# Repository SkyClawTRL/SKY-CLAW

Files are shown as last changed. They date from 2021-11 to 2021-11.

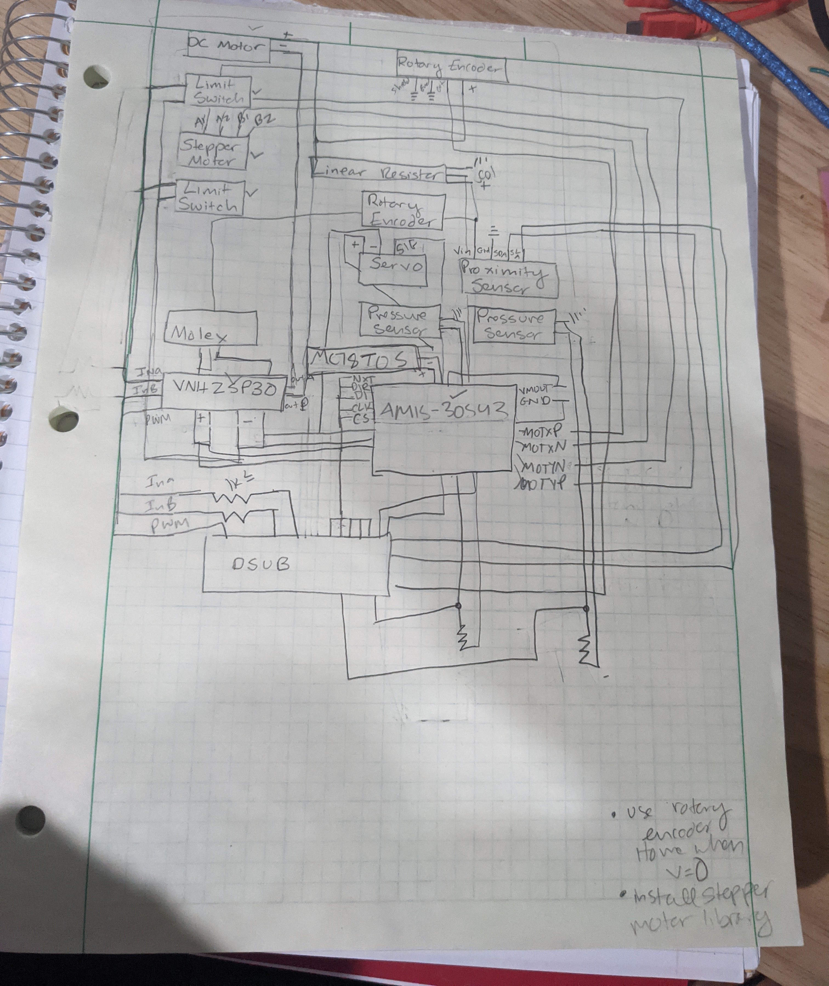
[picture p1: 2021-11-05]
Schematics and Datasheets/CONTROL BOX SCHEMATIC.jpg

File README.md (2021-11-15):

# SKY-CLAW
Fully Open Source Gantry-Style Robotic Gripper
The claw is a four degree of freedom robot equipped with multiple sensors and actuators. The four degrees of freedom are horizontal translation, vertical translation, (passive) rotation, and grasping motion. The claw is similar to a gantry crane that might be found at a construction site or in a warehouse. The purpose of this project is to provide an educational platform for teaching mechatronics. The benefits of this platform are:
  a) It provides a diverse set of sensors and actuators:
       i) Sensors: limit switches, proximity sensor, linear potentiometer, rotary encoders.
       ii) Actuators: Stepper motor, brushed DC motor, servo
  b) It is 100% open source and uses common commercial off-the-shelf components and complete solid models of all parts including drawings of custom-made parts.
  c) All custom-made components are easy to manufacture. If a student breaks it, he or she can also repair it.

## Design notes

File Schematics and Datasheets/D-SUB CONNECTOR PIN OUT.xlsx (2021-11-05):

1 | Proximity Sensor | SDA (Blue)
2 | Servo | Positive (Yellow)
3 | VNH25P30 Driver | PWM (Blue)
4 | VNH25P30 Driver | In A (Green)
5 | VNH25P30 Driver | In B (White)
6 | AMIS-30543 Driver | Nxt/Step (Blue)
7 | AMIS-30543 Driver | DIR (Blue)
8 | AMIS-30543 Driver | CLK (Green)
9 | AMIS-30543 Driver | DI (Green)
10 | AMIS-30543 Driver | CS ( Green)
11 | Pressure Sensor 1 | Voltage Divider (Green)
12 | Pressure Sensor 2 | Voltage Divider (White)
13 | Proximity Sensor | SCL (white)
14 | nc | nc
15 | nc | nc
16 | nc | nc
17 | nc | nc
18 | nc | nc
19 | nc | nc
20 | Ground | Black
21 | Linear Resistor | Col (White)
22 | Top Rotary Encoder | Channel A (black)
23 | Top Rotary Encoder | Channel B (white)
24 | Claw Rotary Encoder | Channel B (White)
25 | Claw Rotary Encoder | Channel A (Black)

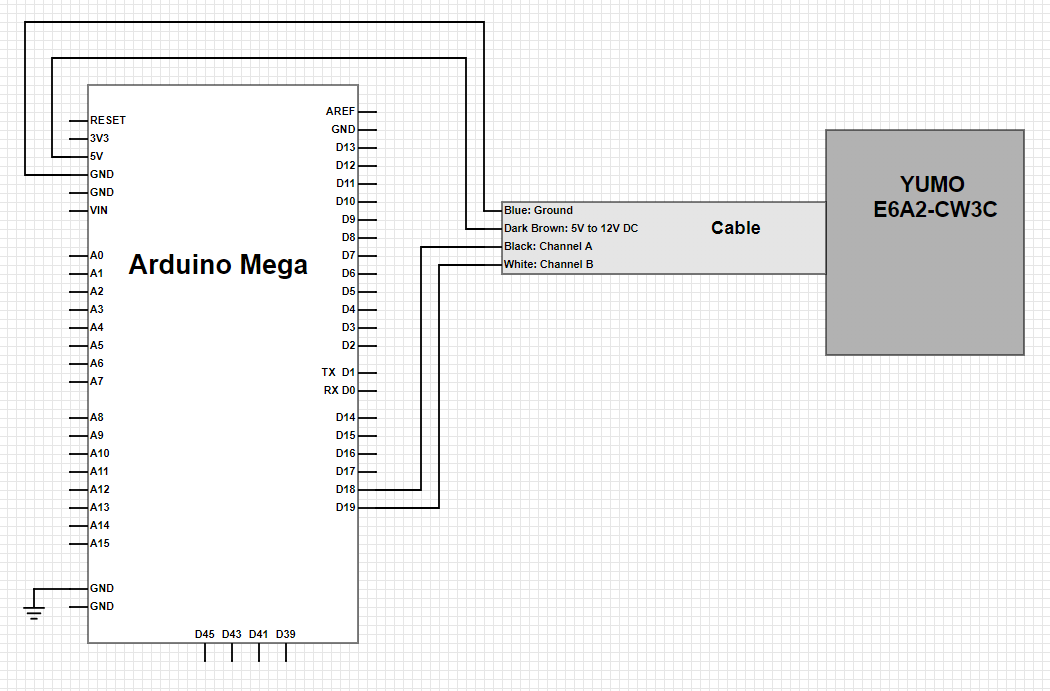
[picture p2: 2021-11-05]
Schematics and Datasheets/Yumo E6A2-CW3C Rotary Encoder Schematic.PNG

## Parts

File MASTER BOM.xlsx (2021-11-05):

PART NUMBER | SUPPLIER | DESCRIPTION | QUANTITY | PRICE | TOTAL COST | NOTES
2191A14 | Mc-Master-Carr | Steel Metric Ball-Nose Plunger with Plastic Nose M6x1 Thread, 6.3-9 lb. Nose Force | 1 | $5.54 | $5.54
4575N23 | Mc-Master-Carr | Light Duty Mounted Ball Bearing with Two-Bolt Flange, Open, for 1/4" Shaft Diameter | 13 | $9.70 | $126.10
47065T101 | Mc-Master-Carr | T-Slotted Framing Single Four Slot Rail, Silver, 1" High x 1" Wide, Solid 4 Feet Long | 2 | $18.05 | $36.10
47065T139 | Mc-Master-Carr | T-Slotted Framing End-Feed Single Nut with Button Head 1/4"-20 Thread Size | 44 | $2.22 | $24.42
47065T236 | Mc-Master-Carr | Silver Corner Bracket, 1" Long for 1" High Rail T-Slotted Framing | 12 | $5.63 | $67.56
57155K336 | Mc-Master-Carr | Stainless Steel Ball Bearing Flanged, Shielded with Extended Inner Ring, Number R168-2Z | 3 | $7.35 | $22.05
6477K58 | Mc-Master-Carr | Two Arm Knob Black Nylon, 1/4"-20 Threaded Through-Hole | 1 | $1.23 | $1.23
6484K454 | Mc-Master-Carr | XL Series Timing Belt, Trade No. 770XL037 3/8" Thick | 1 | $20.26 | $20.26
7565K46 | Mc-Master-Carr | Cable Holders Adhesive-Back, Nylong, 1" Long x 3/4" Wide x 7/8" High | 7 | $9.05 | $9.05
8505K754 | Mc-Master-Carr | Scratch-Resistant Acrylic, 12" x 12" x 1/4" | 1 | $10.78 | $10.78
8632T141 | Mc-Master-Carr | D-Profile Rotary Shaft 1045 Carbon Steel, 1/4" Diameteer, 24" Long | 5 | $16.50 | $16.50
8975K468 | Mc-Master-Carr | 6061 Aluminum 3/8" Thick x 2-1/2" Wide Sheet and Bar 3 Feet Long | 3 | $26.37 | $79.11
9001K62 | Mc-Master-Carr | 6063 Aluminum U-Channel 1/8" Wall Thickness, 2" High x 1-1/2" Wide | 1 | $43.88 | $43.88
90480A007 | Mc-Master-Carr | Low-Strength Steel Hex Nut Zinc-Plated, 6-32 Thread Size | 74 | $1.28 | $1.28
90633A005 | Mc-Master-Carr | Low-Strength Steel Thin Nylon-Insert Locknut Zinc-Plated, 4-40 Thread Size | 2 | $3.71 | $3.71
90695A038 | Mc-Master-Carr | Steel Thin Hex Nut Medium-Strength, Zinc-Plated, M6x1mm Thread | 2 | $3.45 | $3.45
90730A003 | Mc-Master-Carr | 18-8 Stainless Steel Narrow Hex Nut 2-56 Thread Size | 2 | $3.66 | $3.66
91239A115 | Mc-Master-Carr | Button Head Hex Drive Screw Black-Oxide Alloy Steel, M3x0.50mm Thread, 10mm Long | 8 | $8.12 | $8.12
91255A539 | Mc-Master-Carr | Button Head Hex Drive Screw Black-Oxide Alloy Steel, 1/4"-20 Thread, 5/8" Long | 18 | $9.78 | $9.78
91292A025 | Mc-Master-Carr | 18-8 Stainless Steel Socket Head Screw M3x0.50mm Thread, 45mm Long | 8 | $12.76 | $12.76
91772A361 | Mc-Master-Carr | Passivated 18-8 Stainless Steel Pan Head Phillips Screw 8-32 Thread, 1-5/8" Long | 4 | $8.85 | $8.85
91772A544 | Mc-Master-Carr | Passivated 18-8 Stainless Steel Pan Head Phillips Screw 1/4"-20 Thread, 1-1/4" Long | 4 | $7.97 | $7.97
91841A005 | Mc-Master-Carr | 18-8 Stainless Steel Hex Nut 4-40 Thread Size | 5 | $2.82 | $2.82
91841A009 | Mc-Master-Carr | 18-8 Stainless Steel Hex Nut 8-32 Thread Size | 38 | $3.46 | $3.46
91845A029 | Mc-Master-Carr | 18-8 Stainless Steel Hex Nut 1/4"-20 Thread Size | 8 | $3.85 | $3.85
92196A149 | Mc-Master-Carr | 18-8 Stainless Steel Socket Head Screw 6-32 Thread Size, 9/16" Long | 8 | $12.65 | $12.65
92196A194 | Mc-Master-Carr | 18-8 Stainless Steel Socket Head Screw 8-32 Thread Size, 1/2" Long | 10 | $6.24 | $6.24
92210A196 | Mc-Master-Carr | 18-8 Stainless Steel Hex Drive Flat Head Screw 8-32 Thread Size, 5/8" Long | 22 | $5.90 | $5.90
92949A079 | Mc-Master-Carr | 18-8 Stainless Steel Button Head Hex Drive Screw 2-56 Thread Size, 3/8" Long | 2 | $6.59 | $6.59
92949A110 | Mc-Master-Carr | 18-8 Stainless Steel Button Head Hex Drive Screw 4-40 Thread Size, 1/2" Long | 3 | $3.38 | $3.38
92949A116 | Mc-Master-Carr | 18-8 Stainless Steel Button Head Hex Drive Screw 4-40 Thread Size, 1" Long | 4 | $4.75 | $4.75
92949A144 | Mc-Master-Carr | 18-8 Stainless Steel Button Head Hex Drive Screw 6-32 Thread Size, 1/4" Long | 4 | $3.45 | $3.45
92949A150 | Mc-Master-Carr | 18-8 Stainless Steel Button Head Hex Drive Screw 6-32 Thread Size, 5/8" Long | 84 | $4.07 | $4.07
92949A153 | Mc-Master-Carr | 18-8 Stainless Steel Button Head Hex Drive Screw 6-32 Thread Size, 1" Long | 18 | $5.42 | $5.42
92949A157 | Mc-Master-Carr | 18-8 Stainless Steel Button Head Hex Drive Screw 6-32 Thread Size, 1-1/2" Long | 2 | $4.58 | $4.58
92949A205 | Mc-Master-Carr | 18-8 Stainless Steel Button Head Hex Drive Screw 8-32 Thread Size, 1-3/4" Long | 4 | $8.66 | $8.66
93330A471 | Mc-Master-Carr | Female Threaded Round Standoff Aluminum, 1/4" OD, 1-1/4" Long, 6-32 Thread Size | 2 | $1.23 | $2.46
93548A550 | Mc-Master-Carr | Zinc-Plated Grade 2 Steel Square-Neck Carriage Bolt Low-Strength, 1/4"-20 Thread Size, 2" Long | 1 | $10.75 | $10.75
94639A297 | Mc-Master-Carr | Off-White Nylon Unthreaded Spacer 1/4" OD, 3/4" Long, for Number 8 Screw Size | 4 | $12.47 | $12.47
94639A298 | Mc-Master-Carr | Off-White Nylon Unthreaded Spacer 1/4" OD, 1" Long, for Number 8 Screw Size | 4 | $13.56 | $13.56
94639A300 | Mc-Master-Carr | Off-White Nylon Unthreaded Spacer 1/4" OD, 3/16" Long, for Number 6 Screw Size | 6 | $10.35 | $10.35
94639A569 | Mc-Master-Carr | Off-White Nylon Unthreaded Spacer 1/2" OD, 1/4" Long, for 1/4" Screw Size | 14 | $11.38 | $11.38
9880K13 | Mc-Master-Carr | 15mm Wide Guide Rail for High-Temperature Sleeve Bearing Carriage 670mm Long | 2 | $122.61 | $245.22
9880K3 | Mc-Master-Carr | High-Temperature Sleeve Bearing Carriage for 15mm Wide Rail | 2 | $54.40 | $108.80
LPM80-180-1(318025)-c | PBC Linear | Nylon Slider | 1 | $25.23 | $25.23
LPM80R-0780 | PBC Linear | Aluminum Rail Y=16mm | 1 | $94.56 | $94.56
LSSSSR-037-0250-FY24 | HaydenKerk | 3/8" Lead Screw | 2 | $51.16 | $102.32
BFWFNR-037-0250-BZ00 | HaydenKerk | Lead Screw Nut | 2 | $16.18 | $32.36
14203S009-SP | HaydenKerk | 24V Brushed DC Motor | 1 | $184.80 | $184.80
2267 | Pololu | NEMA 17 Stepper Motor | 1 | $17.95 | $17.95
1212 | Pololu | MC33926 Motor Driver Carrier | 1 | $17.95 | $17.95
744-SP-L-0750-2033ST | Mouser | Linear Resistor | 1 | $45.07 | $45.07
782-A000067 | Mouser | Arduino Mega | 1 | $38.50 | $38.50
COM-10932 | SparkFun | Yumo E6A2-CW3C | 2 | $44.95 | $89.90
COM-11992 | SparkFun | Momentary Button | 2 | $0.95 | $1.90
ROB-12156 | SparkFun | Timing Belt - XL (per foot) 6 Feet Long | 6 | $3.59 | $21.54
ROB-12251 | SparkFun | Shaft Coupler - 1/4" to 1/4" | 4 | $4.99 | $19.96
ROB-12325 | SparkFun | Shaft Coupler - 1/4" to 5mm | 1 | $4.99 | $4.99
ROB-12347 | SparkFun | Servo Block Kit - Hitec Standard (Hub Shaft) | 1 | $26.99 | $26.99
ROB-12488 | SparkFun | Set Screw Hub | 4 | $4.99 | $19.96
ROB-12493 | SparkFun | Shaft Coupler - 1/4" to 4mm | 1 | $4.99 | $4.99
ROB-13597 | SparkFun | Timing Pulley - Shaft Mount (15T; 0.25" Bore) | 5 | $8.95 | $44.75
SEN-08712 | SparkFun | FlexiForce Pressure Sensor - 25lbs. | 2 | $21.95 | $43.90
35645S00 | Servo City | HS-5645MG Servo | 1 | $44.99 | $44.99
SC508 | Servo City | Servo Connector Pack Hitec Male/Female Set | 1 | $2.99 | $2.99
SW22JT | Servo City | Super Duty Servo Wire 50 Feet Long | 1 | $12.99 | $12.99
1508102 | Home Depot | 1/4 in x 2 ft x 2 ft MDF Panel | 2 | $8.85 | $17.70
466 | Adafruit | VCNL4010 Proximity Sensor | 1 | $7.50 | $7.50
SMAKN TB6600 | Amazon | 4A 40V 57/86 Stepper Motor Driver | 1 | $14.90 | $14.90
Ginsco | Amazon | 580 pieces Heat Shrink Tubing Kit 6 Colors 11 Sizes | 1 | $5.99 | $5.99
Striveday | Amazon | Flexible Silicon Wire 22awg Electric Wire 22 Gauge Copper 330V | 1 | $15.99 | $15.99
EDGELEC | Amazon | Multicolored Breadboard Jumper Wires Assorted Kit 120 pieces | 1 | $5.77 | $5.77
 |  |  |  | Total | $1979.41 | Pricing was done on 7/11/2021

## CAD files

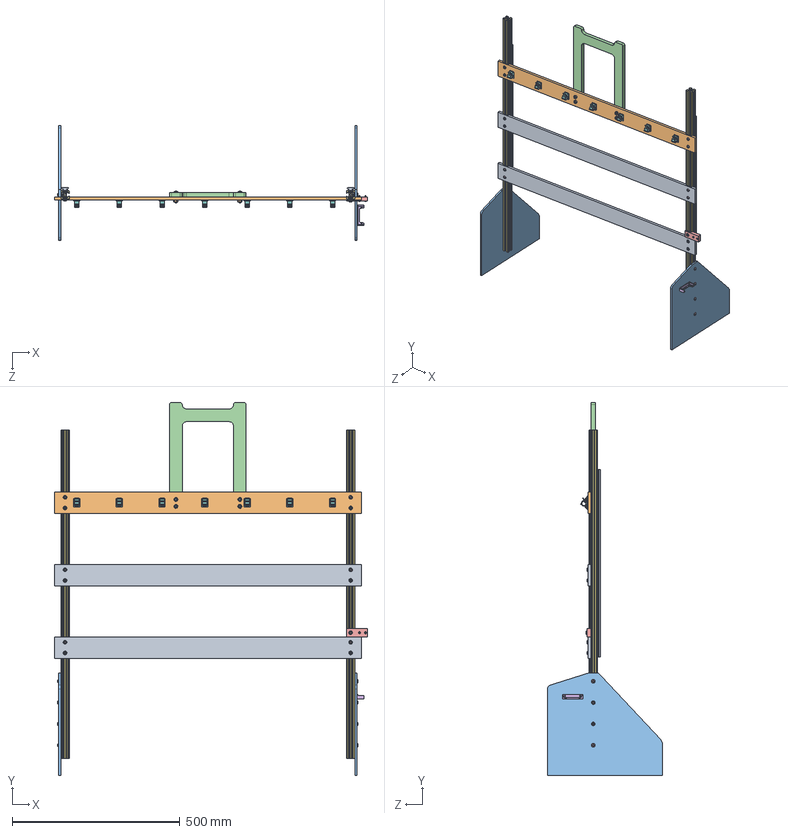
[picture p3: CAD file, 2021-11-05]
SUBASSEMBLIES/FRAME ASSEMBLY.SLDASM
933.2 x 1111.2 x 342.9 mm
FRAME BRACE x 2
FRAME BRACE TOP
FOOT x 2
HANDLE
CABLE CARRIER CONNECTOR VERTICAL
DSUB MOUNT
47065T101_ALUMINUM T-SLOTTED FRAMING EXTRUSION x 2
7565K460_CABLE HOLDERS x 7
9880K135_SLEEVE BEARING CARRIAGE x 2
91845A029_TYPE 18-8 STAINLESS STEEL HEX NUT x 4
91772A544_18-8 SS PAN HEAD PHILLIPS MACHINE SCREW x 4
92949A150_18-8 SS BUTTON-HEAD SOCKET CAP SCREW x 2
47065T139_ALUMINUM T-SLOTTED FRAMING EXTRUSION x 35

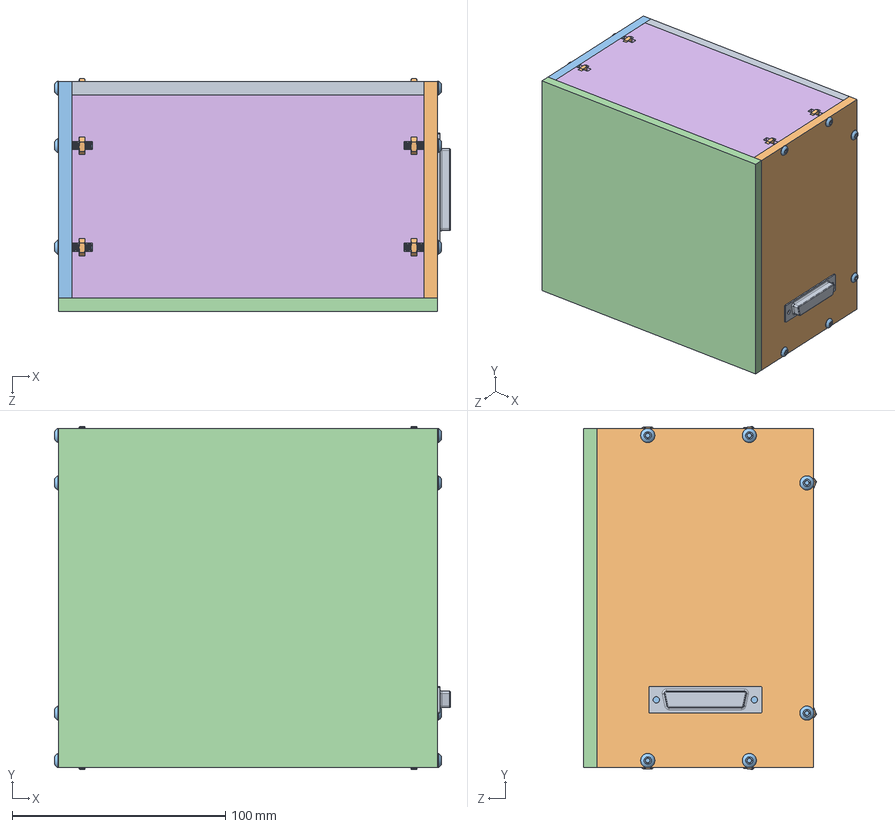
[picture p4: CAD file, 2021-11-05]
SUBASSEMBLIES/CONTROL BOX.SLDASM
185.7 x 160.9 x 109.3 mm
CONTROL BOX BACK PANEL
CONTROL BOX RIGHT PANEL
CONTROL BOX LEFT PANEL
CONTROL BOX FRONT PANEL
CONTROL BOX BOTTOM PANEL
CONTROL BOX TOP PANEL
VNH3SP30 Motor Driver Carrier MD01B x 2
PCB
D-SUB CONNECTOR
90480A007_LOW-STRENGTH STEEL HEX NUT x 12
92949A150_18-8 SS BUTTON-HEAD SOCKET CAP SCREW x 12

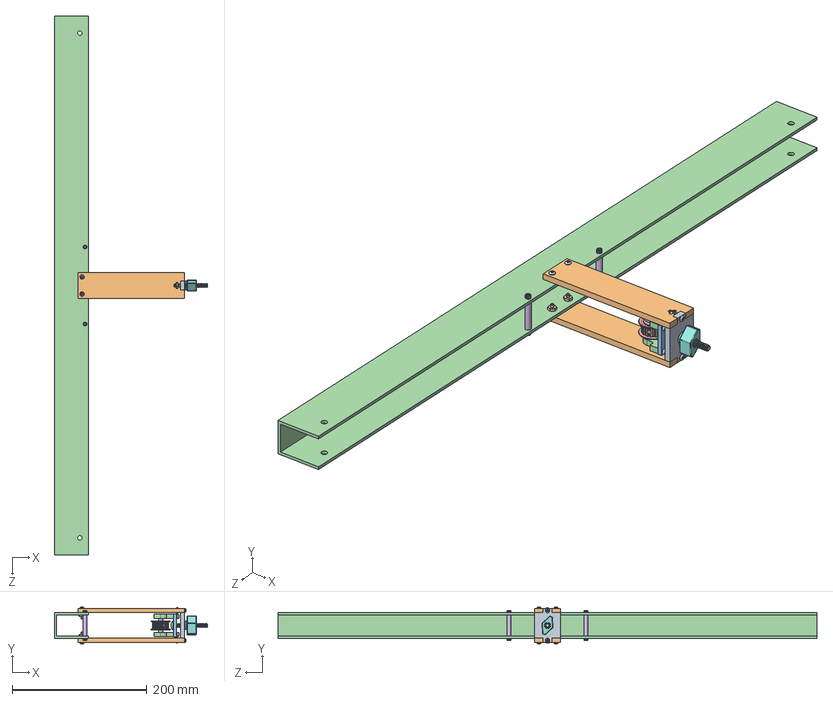
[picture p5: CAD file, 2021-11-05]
SUBASSEMBLIES/U-CHANNEL ASSEMBLY.SLDASM
227.8 x 54.5 x 800.1 mm
TENSIONER SUPPORT BACK
TENSIONER SUPPORT BASE x 2
TENSIONER PLATE
TENSIONER BEARING x 2
ROB-13597 TIMING PULLEY
8632T141_D-SHAFT PROFILE 1.3125 LG
tensioner bolt_93548A550
tensioner knob 6477K580
92949A150_18-8 SS BUTTON-HEAD SOCKET CAP SCREW x 6
90480A007_LOW-STRENGTH STEEL HEX NUT x 6
caseing screw 92185A164 x 4
TENSIONER U-CHANNEL
92196A149_18-8 STAINLESS STEEL SOCKET HEAD SCREW x 4
93330A471_ALUM FEM THRDED ROUND STANDOFF x 2

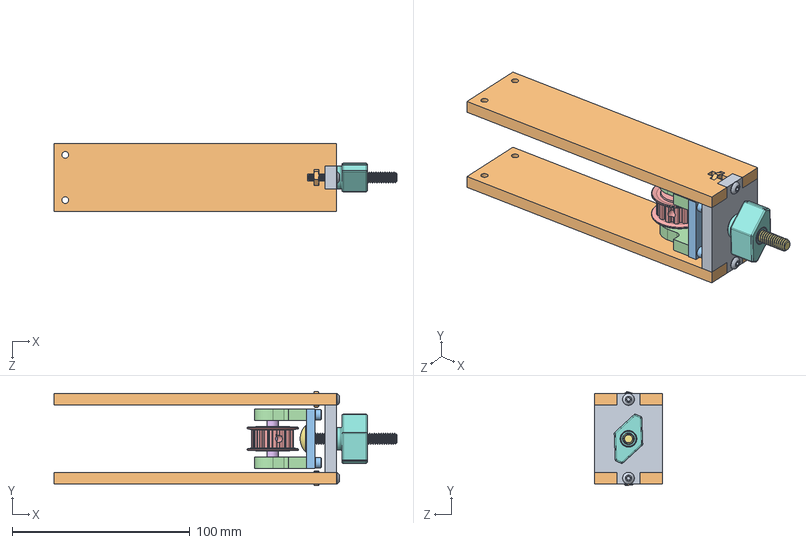
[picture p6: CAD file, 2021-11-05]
SUBASSEMBLIES/TENSIONER ASSEMBLY.SLDASM
192.9 x 52.9 x 38.1 mm
TENSIONER SUPPORT BACK
TENSIONER SUPPORT BASE x 2
TENSIONER PLATE
TENSIONER BEARING x 2
ROB-13597 TIMING PULLEY
8632T141_D-SHAFT PROFILE 1.3125 LG
tensioner bolt_93548A550
tensioner knob 6477K580
92949A150_18-8 SS BUTTON-HEAD SOCKET CAP SCREW x 2
90480A007_LOW-STRENGTH STEEL HEX NUT x 2
caseing screw 92185A164 x 4

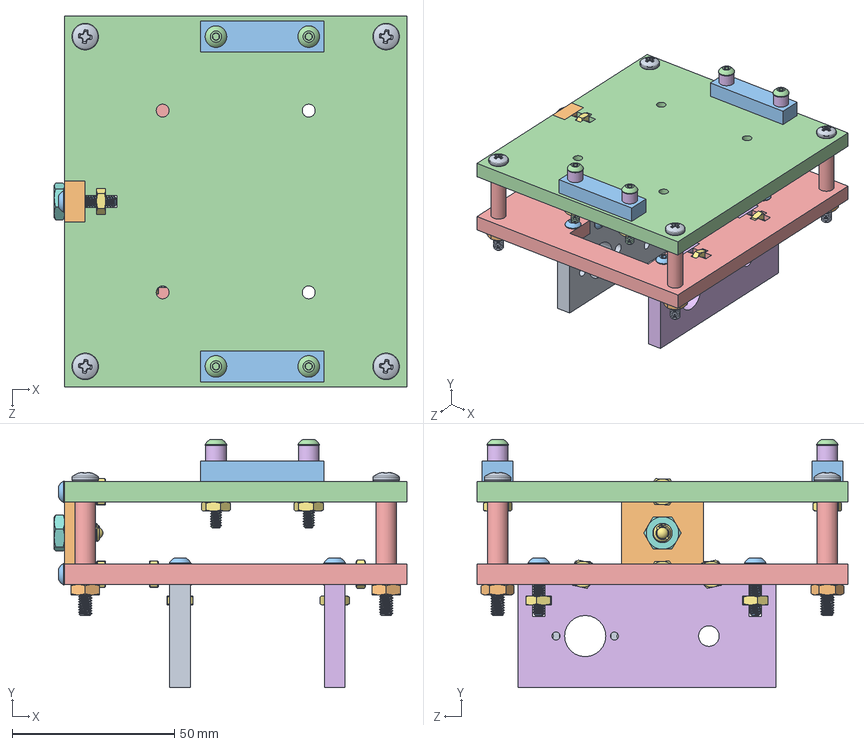
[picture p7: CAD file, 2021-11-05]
SUBASSEMBLIES/GRIPPER MOUNT ASSEMBLY.SLDASM
108.6 x 76.5 x 114.3 mm
CLAW BEARING MOUNT
CLAW LINEAR POTENTIOMETER PIN MOUNT
BELT CLAMP x 2
CLAW MOUNTING PLATE CARRIAGE
CLAW MOUNTING PLATE
CLAW BEARING MOUNT BACK
90480A007_LOW-STRENGTH STEEL HEX NUT x 14
90695A038_CLASS 04 STEEL THIN HEX NUT - DIN 439B x 2
91772A361_18-8 SS PAN HEAD PHILLIPS MACHINE SCREW x 4
91841A009_TYPE 18-8 STAINLESS STEEL HEX NUT x 4
92949A150_18-8 SS BUTTON-HEAD SOCKET CAP SCREW x 10
92949A153_18-8 SS BUTTON-HEAD SOCKET CAP SCREW x 4
94639A297_NYLON UNTHREADED SPACERS x 4
94639A300_OFF-WHITE NYLON UNTHREADED SPACER (1) x 4
2191A14_STEEL METRIC BALL-NOSE PLUNGER W PLASTIC NOSE

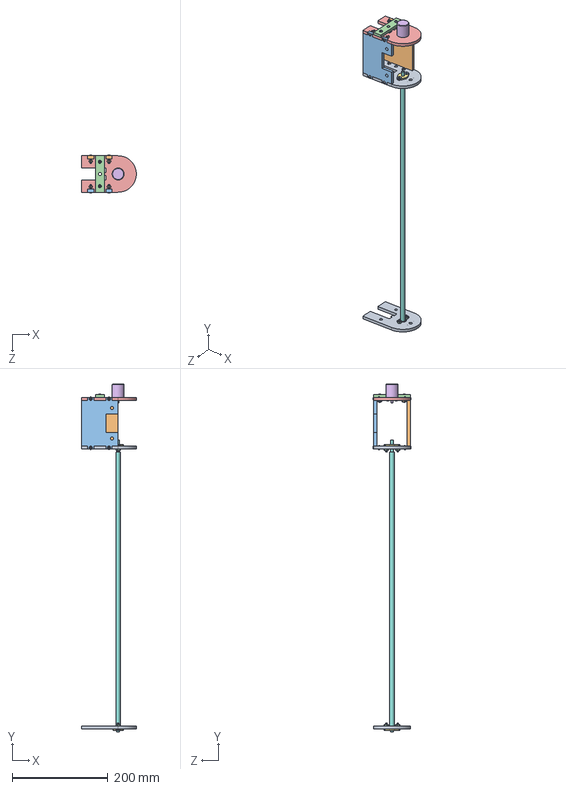
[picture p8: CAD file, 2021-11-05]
SUBASSEMBLIES/VERTICAL TRANSLATION HOUSING ENCODER.SLDASM
114.3 x 726.4 x 79.9 mm
PULLY GUIDE HOUSING BASE x 2
PULLY GUIDE HOUSING OUTER WALL
PULLY GUIDE HOUSING INNER WALL
PULLY GUIDE HOUSING TOP CAP
PULLY GUIDE HOUSING TOP
COM-10932
4575N230_LIGHT DUTY TWO-BOLT FLANGE-MOUNTED BALL BRNG x 2
LEAD SCREW
92949A150_18-8 SS BUTTON-HEAD SOCKET CAP SCREW x 10
90480A007_LOW-STRENGTH STEEL HEX NUT x 10
92210A196_18-8 STAINLESS STEEL FLAT-HEAD SCKT CAP SCREW x 4
91841A009_TYPE 18-8 STAINLESS STEEL HEX NUT x 4
91239A115_CLASS 10.9 STL BUTTON-HEAD SOCKET CAP SCREW x 2

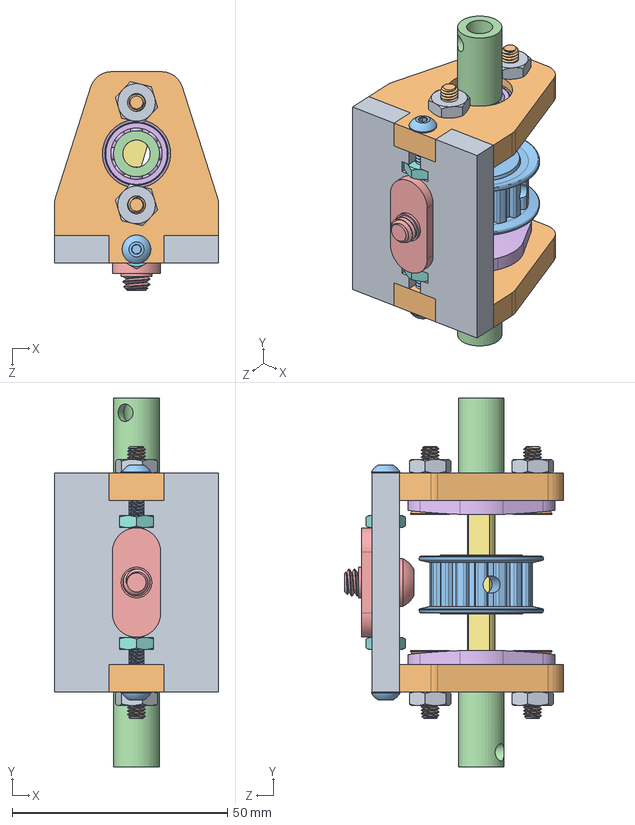
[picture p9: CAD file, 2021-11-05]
SUBASSEMBLIES/PULLEY BEARING GUIDE.SLDASM
38.1 x 85.7 x 50.8 mm
PULLEY BEARING GUIDE BACK
PULLEY BEARING GUIDE BASE x 2
ROB-13597 TIMING PULLEY
ROB-12251 x 2
47065T139_ALUMINUM T-SLOTTED FRAMING EXTRUSION
4575N230_LIGHT DUTY TWO-BOLT FLANGE-MOUNTED BALL BRNG x 2
8632T141_D-PROFILE SHAFT 2.625 LG
90480A007_LOW-STRENGTH STEEL HEX NUT x 2
91841A009_TYPE 18-8 STAINLESS STEEL HEX NUT x 4
92210A196_18-8 STAINLESS STEEL FLAT-HEAD SCKT CAP SCREW x 4
92949A150_18-8 SS BUTTON-HEAD SOCKET CAP SCREW x 2

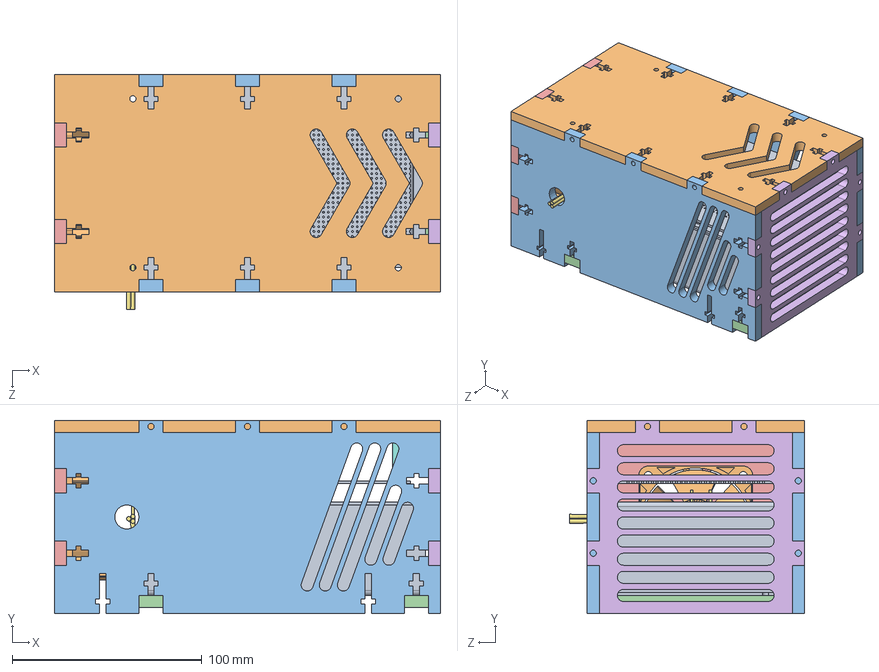
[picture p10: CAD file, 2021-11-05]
SUBASSEMBLIES/POWER SUPPLY COVER.SLDASM
203.2 x 101.6 x 123.5 mm
POWER SUPPLY
POWER SUPPLY FRONT COVER
POWER SUPPLY SIDE COVER x 2
POWER SUPPLY SIDE SUPPORT x 2
POWER SUPPLY TOP COVER
POWER SUPPLY BOTTOM COVER
POWER SUPPLY WIRES
94639A298_OFF-WHITE NYLON UNTHREADED SPACER x 4
PROTOBOARD
1939K580_DC EQUIPMENT COOLING FAN

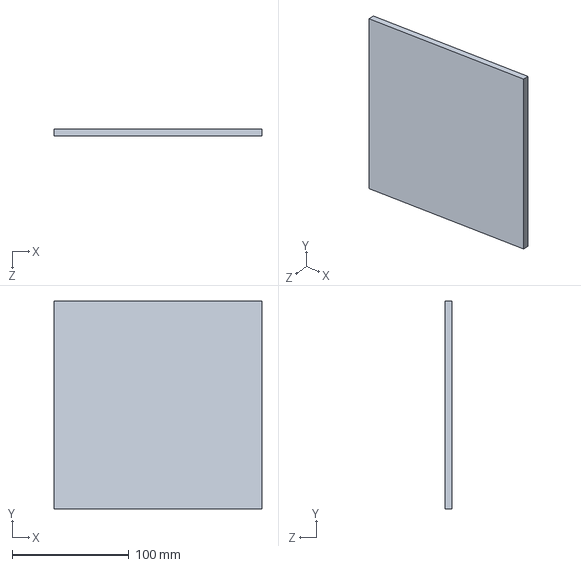
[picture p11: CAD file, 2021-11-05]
FAB/CONTROL BOX FRONT PANEL.SLDPRT
177.8 x 177.8 x 6.35 mm

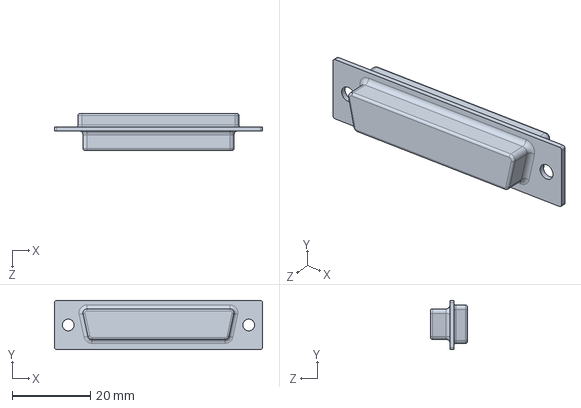
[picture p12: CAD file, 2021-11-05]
HARDWARE/D-SUB CONNECTOR.SLDPRT
53.0 x 12.5 x 9.50 mm

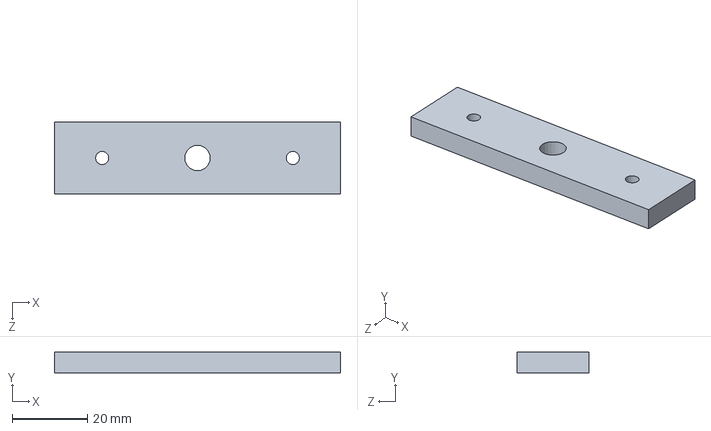
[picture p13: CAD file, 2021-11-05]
FAB/PULLY GUIDE HOUSING TOP CAP.SLDPRT
76.2 x 5.59 x 19.1 mm

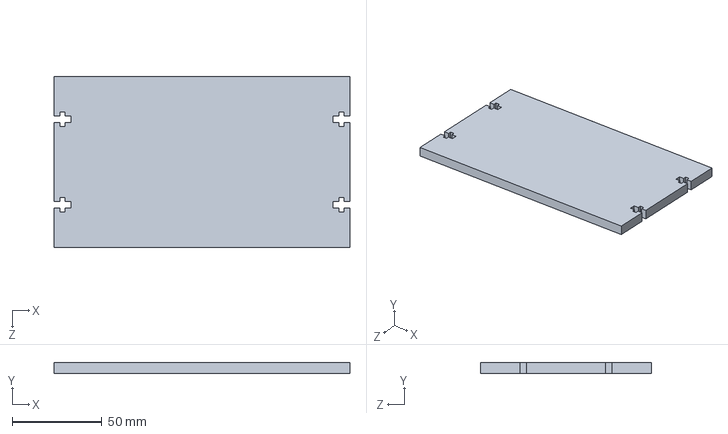
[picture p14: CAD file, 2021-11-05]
HARDWARE/CONTROL BOX BOTTOM PANEL.SLDPRT
165.1 x 6.35 x 95.2 mm

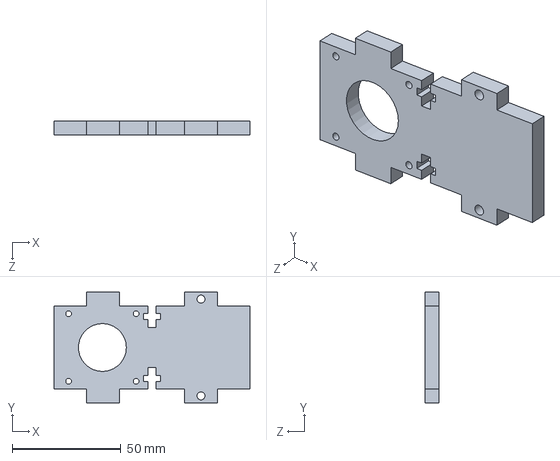
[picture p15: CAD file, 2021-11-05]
FAB/HORIZONTAL SHAFT SUPPORT MOTOR SIDE.SLDPRT
90.0 x 50.8 x 6.35 mm

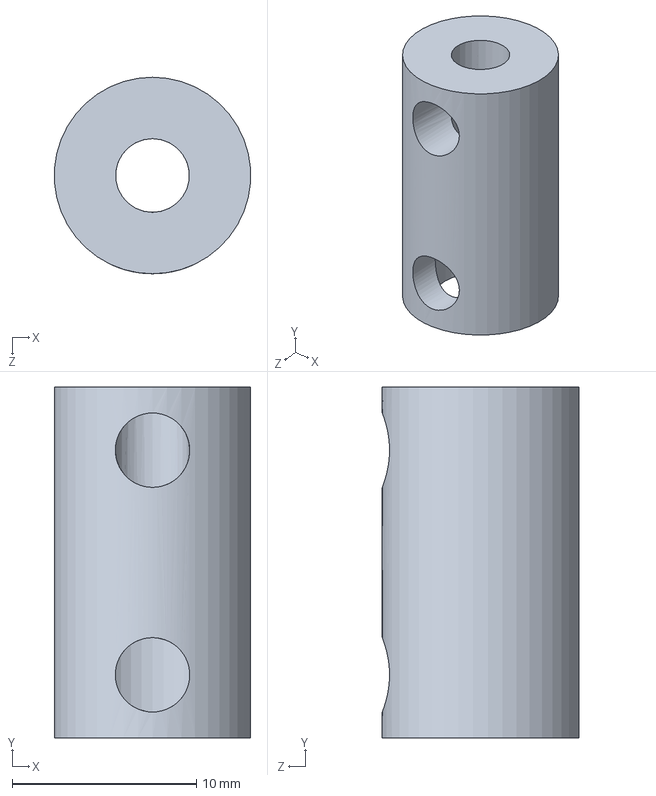
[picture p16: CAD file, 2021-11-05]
HARDWARE/ROB-12493.SLDPRT
10.6 x 19.1 x 10.7 mm

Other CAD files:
FAB/CONTROL BOX BACK PANEL.SLDPRT
HARDWARE/standoff.SLDPRT
FAB/DSUB MOUNT.sldprt
FAB/CONTROL BOX TOP PANEL.SLDPRT
FAB/3D PRINTED TENSIONER.SLDPRT
FAB/BEARING PLATE.sldprt
FAB/BELT CLAMP.SLDPRT
FAB/CABLE CARRIER CONNECTOR VERTICAL.sldprt
FAB/CLAW BEARING MOUNT BACK.SLDPRT
FAB/CLAW BEARING MOUNT.SLDPRT
FAB/CLAW LINEAR POTENTIOMETER PIN MOUNT.SLDPRT
FAB/CLAW MOUNTING PLATE CARRIAGE.SLDPRT
FAB/CLAW MOUNTING PLATE.SLDPRT
FAB/CONNECTING ROD.SLDPRT
FAB/CONTROL BOX LEFT PANEL.SLDPRT
FAB/CONTROL BOX RIGHT PANEL.SLDPRT
FAB/ETHERNET ADAPTER.SLDPRT
FAB/FOOT.SLDPRT
FAB/GRIPPER CENTER END EFFECTOR.SLDPRT
FAB/GRIPPER END EFFECTOR CONNECTING LINK.sldprt
FAB/GRIPPER END EFFECTOR.SLDPRT
FAB/HANDLE.SLDPRT
FAB/HORIZONTAL CABLE CARRIER ADAPTER.SLDPRT
FAB/HORIZONTAL CARRIAGE BASE MOTOR SIDE.SLDPRT
FAB/HORIZONTAL CARRIAGE BASE SPINDLE SIDE.SLDPRT
FAB/HORIZONTAL CARRIAGE VERTICAL MOTOR SIDE.SLDPRT
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

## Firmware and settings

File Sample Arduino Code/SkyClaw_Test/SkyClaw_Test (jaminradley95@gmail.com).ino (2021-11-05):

/*
  Sky Claw Test
  Author: Ben Bradley
  Date: 02/01/2018

  Version:
  1. Stepper Motor Control
  2. Vertical Motor and Encoder Control
  3. Horizontal Potentiometer readings
*/

/*
  Stepper Motor variables for DRV8825
  https://www.pololu.com/product/2133

  Microstepping pinout
  M0  M1  M2  Microstep
  0   0   0   Full
  1   0   0   1/2
  0   1   0   1/4
  1   1   0   1/8
  0   0 	1   1/16
  1   0 	1   1/32
  0   1 	1   1/32
  1   1 	1   1/32
*/

#define stpStepPin 53
#define stpDirPin 52
#define stpM0Pin 51
#define stpM1Pin 50
#define stpM2Pin 49
//#define stpFaultPin 48  //Pin left NC
//#define stpReset 47  //Pin left NC

volatile long stpStepCount = 0;
bool stpDir = 0;  //0: CW  1: CCW

/*
  Horizontal Soft Potentiometer Feedback
  http://www.mouser.com/ProductDetail/Spectra-Symbol/SP-L-0750-203-3-ST/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
*/

#define horPotPin A0

/*
  Vertical Motor Variables for L298N wired in parallel
  http://www.bristolwatch.com/L298N/index.htm

  In1 high In2 low: CW DOWN In1 low In2 high: CCW UP
*/
#define vertMotIn1 46   //pin 46
#define vertMotIn2 45   //pin 45
#define vertMotEn 5    // PWM input for motor PE3

bool vertMotDir = 0;  //0: CW down 1: CCW up
bool * dcnt = &vertMotDir;

/*
  Vertical Encoder Variables
  https://www.sparkfun.com/products/10932
*/
#define vertEnA 3
#define vertEnB 2

volatile long vertCnt = 0;
long * cpnt = &vertCnt;
long target = 38401;
long * tpnt = &target;

int vertTravCnt = 0;
int vertRevCnt = 400;  //Counts per rev



/*
  Vertical Limit Switches
*/
#define limSw1 42
#define limSw2 41

//Register manipulation macros
#define SETBIT(REG, nbit) (REG |= (1 << nbit))
#define TOGGLEBIT(REG, nbit) (REG ^= (1 << nbit))
#define CLEARBIT(REG, nbit) (REG &= ~(1 << nbit))



int incomingByte = 0;

void setup() {

  //Horizontal Stepper Motor
  pinMode(stpStepPin, OUTPUT);
  pinMode(stpDirPin, OUTPUT);
  pinMode(stpM0Pin, OUTPUT);
  pinMode(stpM1Pin, OUTPUT);
  pinMode(stpM2Pin, OUTPUT);
  //pinMode(stpFaultPin, INPUT_PULLUP);   //Used for software detection of overtemp or overcurrent

  //Set stepper driver microstep mode
  digitalWrite(stpM0Pin, LOW);
  digitalWrite(stpM1Pin, HIGH);
  digitalWrite(stpM2Pin, LOW);

  //Horizontal Potentiometer Pin
  pinMode(horPotPin, INPUT);

  //Vertical Motor
  //DDRL |= (1 << vertMotIn1);  // Set pin 46 as output
  //DDRL |= (1 << vertMotIn2);  // Set pin 45 as output
  pinMode(vertMotIn1, OUTPUT);
  pinMode(vertMotIn2, OUTPUT);
  pinMode(vertMotEn, OUTPUT);

  //Vertical Encoder
  pinMode(vertEnA, INPUT_PULLUP);
  pinMode(vertEnB, INPUT_PULLUP);

  attachInterrupt(digitalPinToInterrupt(vertEnA), enA, RISING);
  attachInterrupt(digitalPinToInterrupt(vertEnB), enB, RISING);

  pinMode(limSw1, INPUT_PULLUP);
  pinMode(limSw2, INPUT_PULLUP);


  Serial.begin(9600);
}

void loop() {

  if (Serial.available() > 0) {
    // read the incoming byte:
    incomingByte = Serial.read();
    if (incomingByte == 114) { //r
      stpStep(400, 1);
    } else if (incomingByte == 117) { //u
      vertMotDir = 1;
      jogVertical(vertMotDir);
    } else if (incomingByte == 100) { //d
      vertMotDir = 0;
      jogVertical(vertMotDir);
    }
  }

  Serial.println(vertCnt);

}

//jogs vertical stage 400 counts in the specified direction
//false: down true: up
void jogVertical(bool dir) {

  if (dir) {
    target = vertCnt + 400;
    while (vertCnt < target) {
      SETBIT(PORTL, 4);
      CLEARBIT(PORTL, 3);
      analogWrite(vertMotEn, 128);
    }
    //Stop motor
    PORTL &= 11100111;
    digitalWrite(vertMotEn, HIGH);

  } else {
    target = vertCnt - 400;
    while (vertCnt > target) {
      SETBIT(PORTL, 3);
      CLEARBIT(PORTL, 4);
      analogWrite(vertMotEn, 128);
    }
    //Stop motor
    PORTL &= 11100111;
    digitalWrite(vertMotEn, HIGH);
  }
}

//Find travel limits of the vertical stage
void verticalHome() {
  if (digitalRead(limSw1) == HIGH && digitalRead(limSw2) == HIGH) {

    //Lower vertical Stage until it reaches the first limit switch
    while (digitalRead(limSw1) == HIGH) {
      digitalWrite(vertMotIn1, HIGH);
      digitalWrite(vertMotIn2, LOW);
      analogWrite(vertMotEn, 128);
    }
    //Stop motor
    analogWrite(vertMotEn, 0);
    //Reset encoder count to zero
    vertCnt = 0;
    vertTravCnt = vertCnt;

    //Raise vertical stage from  switch
    while (vertCnt < 200) {
      digitalWrite(vertMotIn1, LOW);
      digitalWrite(vertMotIn2, HIGH);
      analogWrite(vertMotEn, 128);
    }

    //Stop motor
    analogWrite(vertMotEn, 0);

    //Approach lower limit switch again slower
    while (digitalRead(limSw1) == HIGH) {
      digitalWrite(vertMotIn1, HIGH);
      digitalWrite(vertMotIn2, LOW);
      analogWrite(vertMotEn, 100);
    }
    //Stop motor
    analogWrite(vertMotEn, 0);

    vertCnt = 0;
    vertTravCnt = vertCnt;

    //Raise vertical stage toward upper limit switch
    while (digitalRead(limSw2) == HIGH) {
      digitalWrite(vertMotIn1, LOW);
      digitalWrite(vertMotIn2, HIGH);
      analogWrite(vertMotEn, 128);
    }
    //Stop motor
    analogWrite(vertMotEn, 0);

    int current = vertCnt;

    //Lower vertical stage from  switch
    while (current - vertCnt < 200) {
      digitalWrite(vertMotIn1, HIGH);
      digitalWrite(vertMotIn2, LOW);
      analogWrite(vertMotEn, 128);
    }
    //Stop motor
    analogWrite(vertMotEn, 0);

    //Approach upper limit switch again slower
    while (digitalRead(limSw2) == HIGH) {
      digitalWrite(vertMotIn1, LOW);
      digitalWrite(vertMotIn2, HIGH);
      analogWrite(vertMotEn, 100);
    }
    //Stop motor
    analogWrite(vertMotEn, 0);

    //Set counts for full vertical travel
    vertTravCnt = vertCnt;

    while (vertCnt > (vertTravCnt * 0.75)) {
      digitalWrite(vertMotIn1, HIGH);
      digitalWrite(vertMotIn2, LOW);
      analogWrite(vertMotEn, 128);
    }
    //Stop motor
    analogWrite(vertMotEn, 0);

  }
}

/*
  Moves the stepper motor a number of steps in the specified direction
*/
void stpStep(int steps, bool dir) {

  if (dir) {
    digitalWrite(stpDirPin, HIGH);
  } else {
    digitalWrite(stpDirPin, LOW);
  }

  if (steps > 0) {

    for (int i = 0; i < steps; i++) {
      digitalWrite(stpStepPin, HIGH);
      delay(5);
      digitalWrite(stpStepPin, LOW);
      delay(5);
    }
  } else {
    Serial.println("Invalid number of steps");
  }
}

void enA() {
  if (digitalRead(vertEnB) == LOW) {
    ++(*cpnt);
  } else {
    --(*cpnt);
  }
}

void enB() {
  if (digitalRead(vertEnA) == LOW) {
    --(*cpnt);
  } else {
    ++(*cpnt);
  }
}

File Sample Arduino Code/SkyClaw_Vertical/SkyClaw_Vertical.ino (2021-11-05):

/*
   SkyClaw Vertical Travel
   Author: Ben Bradley
*/

#define in1 8
#define inv 9
#define upLimSwitch 13

#define MOTOR_1_PWM in1 // Motor 1 PWM Speed
#define MOTOR_1_DIR inv // Motor 1 Direction

#define vertEnA 2
#define vertEnB 3

//PWM values for motor speed
float Vcal = 0;
int Vmin = 70;
int Vmax = 255;

//Homing command speed
int calibSpeed = 80;

//Encoder resolution
int resolution = 400;

//User specified vertical positon, 0 at top, 40 at bottom
int inPos = 0;
int desPos = 0;
int oldPos = -1;
int newPos = 0;
int posCh = 0;

volatile long enCount = 0;

//Acceleration constant
int ACC = 15000;

//Screw pitch, revolutions/vertical travel
float ratio = 0.25; //in/rev

long x;
long xOld = 0;
// the actual values for "fast" and "slow" depend on the motor
//float Speed=150; // arbitrary fast speed PWM duty cycle
int PWM;

//Counts Deadband
int dx = 20;


void setup() {
  Serial.begin(115200);

  pinMode( MOTOR_1_DIR, OUTPUT );
  pinMode( MOTOR_1_PWM, OUTPUT );
  digitalWrite( MOTOR_1_DIR, LOW );
  digitalWrite( MOTOR_1_PWM, LOW );

  pinMode(upLimSwitch, INPUT_PULLUP);

  attachInterrupt(digitalPinToInterrupt(vertEnA), enA, RISING);
  attachInterrupt(digitalPinToInterrupt(vertEnB), enB, RISING);

}

void loop() {

  //Send gantry up to top limit switch
  
  if (digitalRead(upLimSwitch) == HIGH) {
    while (digitalRead(upLimSwitch) == HIGH) {
      digitalWrite( MOTOR_1_DIR, HIGH ); // direction = reverse
      analogWrite( MOTOR_1_PWM, calibSpeed ); // PWM speed
      //Serial.println("In loop");
    }

    digitalWrite( MOTOR_1_DIR, HIGH);
    digitalWrite( MOTOR_1_PWM, LOW );
    
    //Set 0 position for encoder
    enCount = 0;
  }

  inPos = 0;
  while (Serial.available() > 0) {
    byte incoming = Serial.read();
    if (incoming >= '0' && incoming <= '9') {
      inPos = (inPos * 10) + (incoming - '0');
      delay(5);
    }
    else {
      Serial.println("\nInvalid Entry! Try Again.\n");
    }
    
    //Calculate travel distance in encoder pulses
    x = ((resolution * inPos) / (ratio));
  }

  boolean run;
  //set current position to current encoder count
  newPos = enCount;
  // Check if motor reaches to the given position-----
  if (newPos != oldPos)
  {
    oldPos = newPos;
    posCh = x - newPos;

    //1st half of the way
    if (abs(((posCh)) * 100) >= 50 * abs(x - xOld))
    {
      Vcal = Vmin + ((Vmax - Vmin) * abs(newPos - xOld)) / ACC;
      PWM = min(Vmax, Vcal);
      // digitalWrite( GLED, HIGH ); digitalWrite( YLED, LOW );digitalWrite( RLED, LOW );
    }
    //2nd half of the way
    else if (abs((posCh) * 100) < 50 * abs(x - xOld))
    {
      Vcal = Vmin + abs(((Vmax - Vmin) * (posCh)) / ACC);
      PWM = min (Vmax, Vcal);
      //digitalWrite( YLED, HIGH );digitalWrite( GLED, LOW );digitalWrite( RLED, LOW );
    }
    //Serial.print(positionCh);
    //Serial.print ("/");
    float height = (newPos * ratio) / 800;
    Serial.print("Drop Down Height= ");
    Serial.println(height);
  }

  do {
    if (newPos < (x - dx)) {
      digitalWrite( MOTOR_1_DIR, LOW ); // direction = forward
      analogWrite( MOTOR_1_PWM, PWM ); // PWM speed
      run = true;
    }
    if (newPos > (x + dx)) {
      digitalWrite( MOTOR_1_DIR, HIGH ); // direction = reverse
      analogWrite( MOTOR_1_PWM, PWM ); // PWM speed
      run = true;
    }
    if (newPos <= (x + dx) && newPos >= (x - dx)) {
      digitalWrite( MOTOR_1_DIR, HIGH);
      digitalWrite( MOTOR_1_PWM, LOW );
      run = false;
      xOld = x;
    }
  } while (abs(x - newPos) <= dx && run == true);

}

void enA() {
  if (digitalRead(vertEnB) == LOW) {
    ++(enCount);
  } else {
    --(enCount);
  }
}

void enB() {
  if (digitalRead(vertEnA) == LOW) {
    --(enCount);
  } else {
    ++(enCount);
  }
}
